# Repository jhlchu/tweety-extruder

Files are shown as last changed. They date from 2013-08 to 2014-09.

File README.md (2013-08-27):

Tweety Extruder
===============

A compact direct-drive extruder for the Prusa i3 Mendel RepRap 3D printer.

Description
-----------

Gain a little extra height on your Prusa i3 with this simple direct drive extruder. Requires an inverted "mini" x-carriage or you can use the Universal 24-to-30mm GT2 X-Carriage also included here.

In contrast to the "Compact Extraptor" design (in my Prusa3 fork) the Tweety is meant to be much simpler. It has no separate mounting and requires no long back-to-front screws. Instead of mounting with nuts on the screw posts, the clamp is secured with screws from the front. The SCAD is highly simplified, as well. All components are aligned with reference to the central point where the gear and bearing grab the filament.

The SCAD is set up by default for a 2engineers 50:1 geared stepper motor, MK7 filament drive gear, 3mm filament, and a 608 idler bearing. As a highly parametric SCAD it should be relatively easy to adapt for your specific motor and dimensional preferences.

Assembly
--------

Print the parts, then connect them in the following order:

* First: Insert M3 locknuts deep into the nut traps in the extruder body.
* Assemble the idler with the axle and a 608 bearing.
* Attach the idler to the body with an M3x20mm bolt or 3mm filament.
* Add idler tensioner shoulder bolts, 2x M3x30mm, with nuts
* Attach the motor to the body with 2x M3x15mm bolts
* Insert the hot-end into the extruder.
* Add a short M3 bolt to the fan mounting hinge.
* Attach the fan to the fan mount.
* Attach the hot-end clamp and fan mount with 2x M3x30mm bolts.
* Attach the assembled extruder to the x-carriage with 3x short M3 bolts.

Customizing the SCAD
--------------------

This SCAD has lots of tunable parameters. You can change the filament width, motor size, idler axle offset, mounting height, and much more. Most parameters can be altered and produce a usable object, but there may be a few that create some weird results. Experiment and let me know if you need help.

As usual, all the parts that will come into contact with the hot-end must be printed in ABS (or any heat-tolerant material).

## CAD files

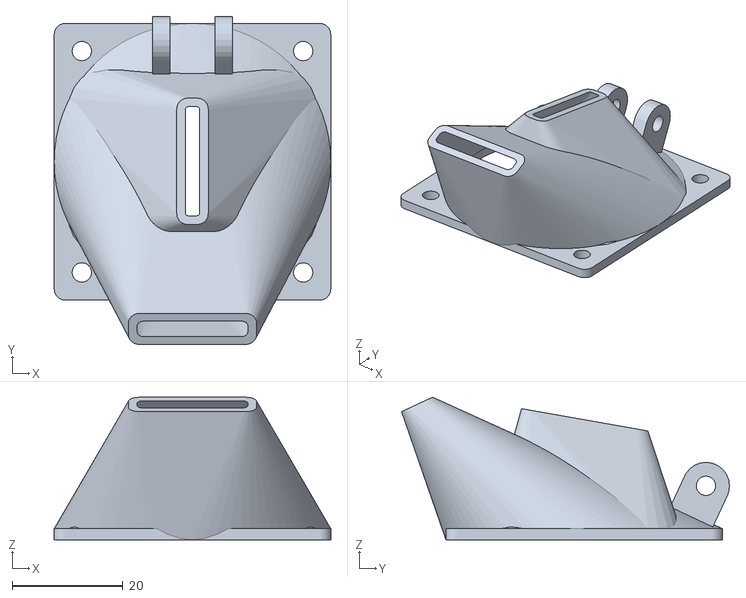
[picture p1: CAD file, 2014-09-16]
output/tweety-fan-duct-only.stl
50.0 x 59.3 x 25.8

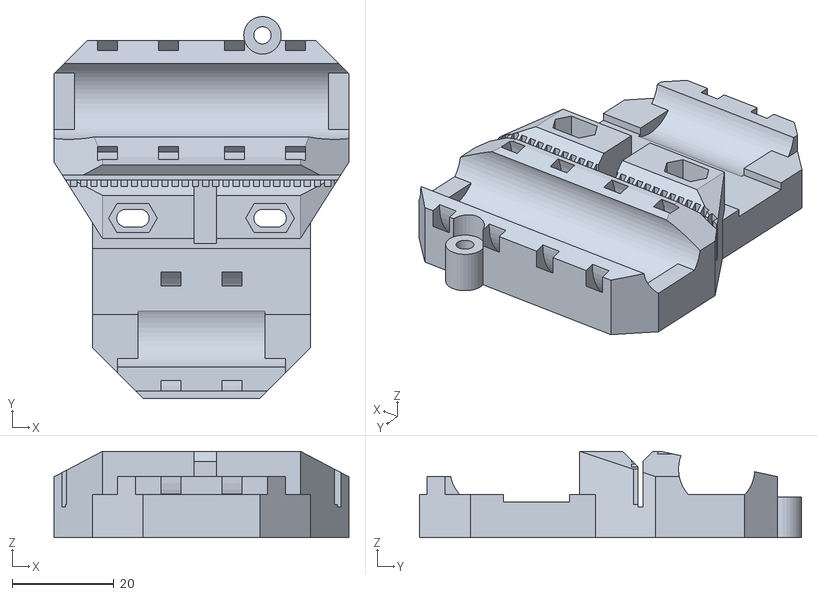
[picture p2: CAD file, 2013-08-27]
x-carriage-24to30-gt2.stl
58.0 x 75.2 x 17.0

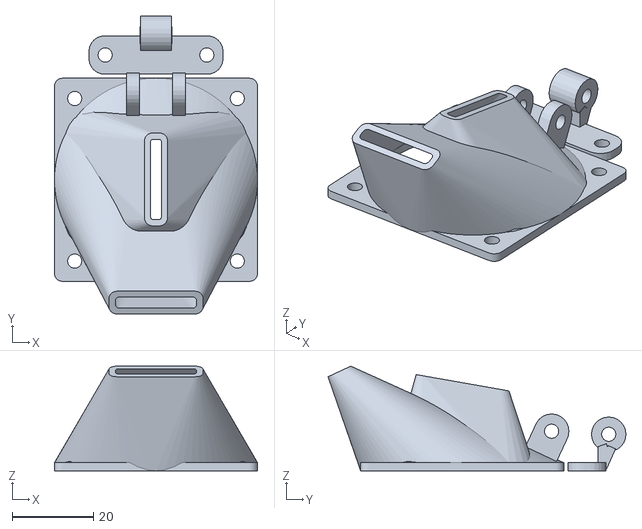
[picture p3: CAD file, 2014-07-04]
output/tweety-fan-duct.stl
50.0 x 73.3 x 25.8

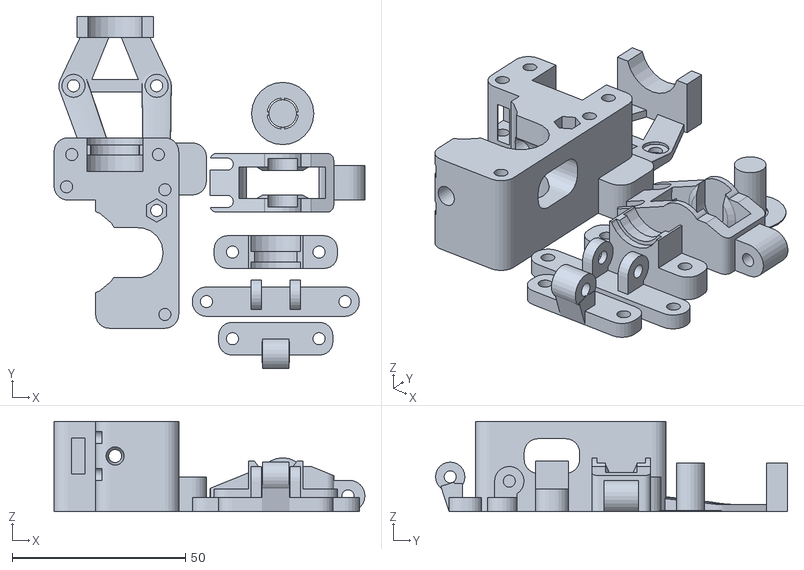
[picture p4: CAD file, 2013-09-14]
output/tweety-plus-all.stl
89.8 x 101.6 x 26.1

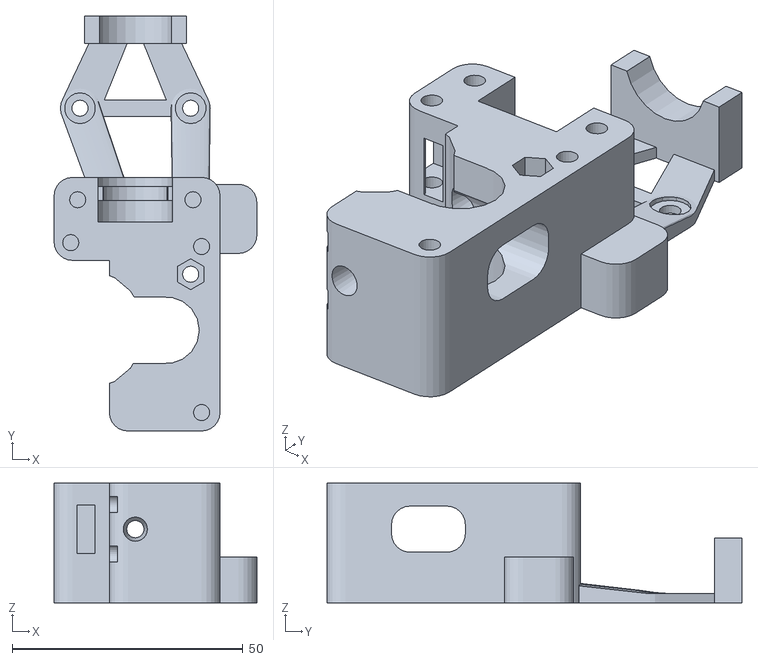
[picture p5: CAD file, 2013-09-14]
output/tweety-plus-body.stl
44.0 x 90.0 x 26.0

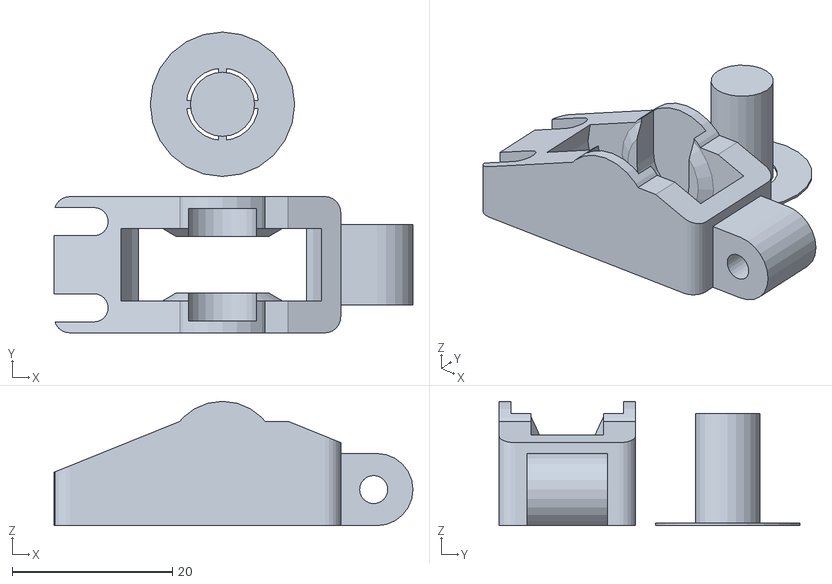
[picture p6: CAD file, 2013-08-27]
output/tweety-idler.stl
44.8 x 37.5 x 15.5

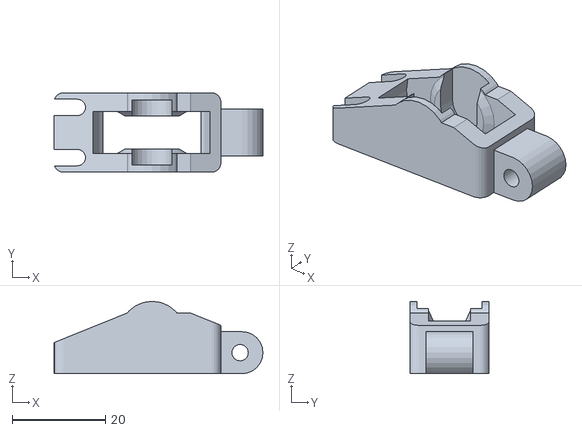
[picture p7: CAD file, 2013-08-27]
output/tweety-idler-no-axle.stl
44.8 x 17.0 x 15.5

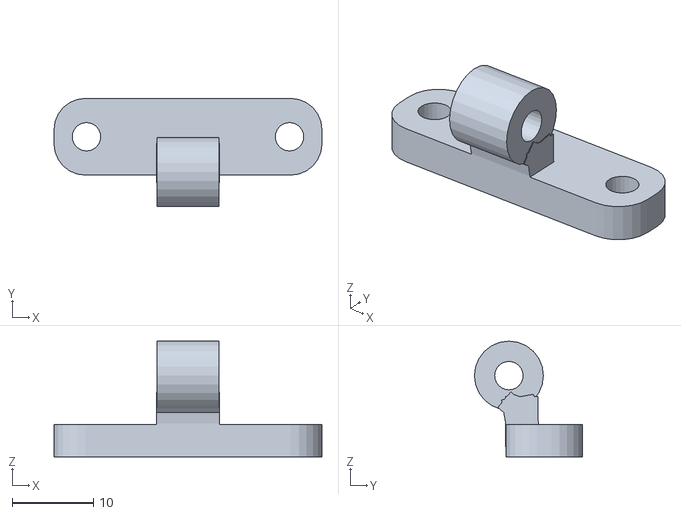
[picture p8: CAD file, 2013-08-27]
output/tweety-fan-hinge.stl
33.0 x 13.3 x 14.3

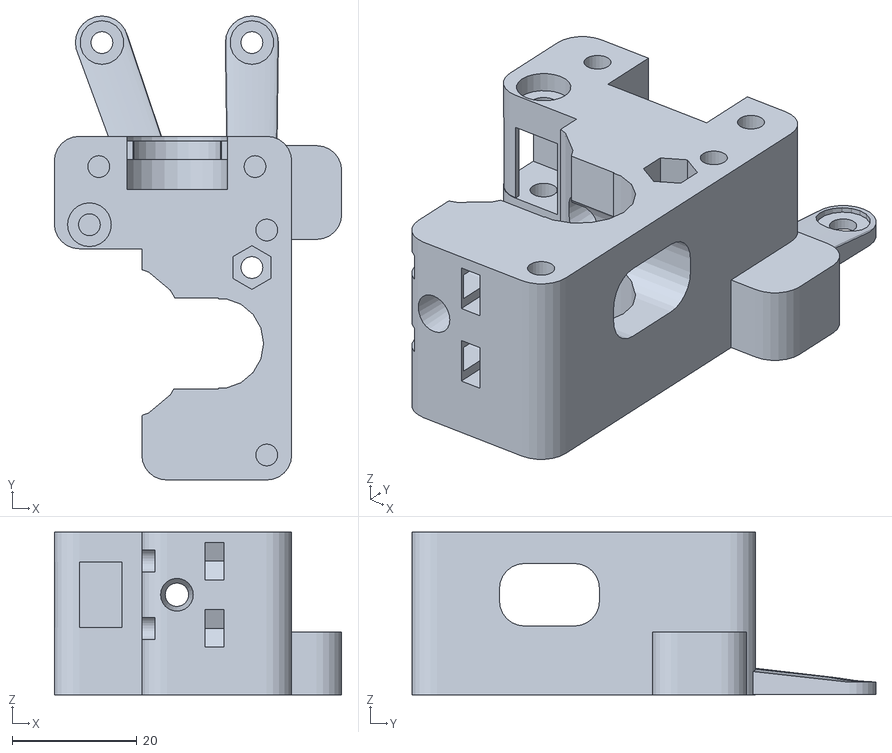
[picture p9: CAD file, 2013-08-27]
output/tweety-body.stl
46.0 x 74.2 x 26.0

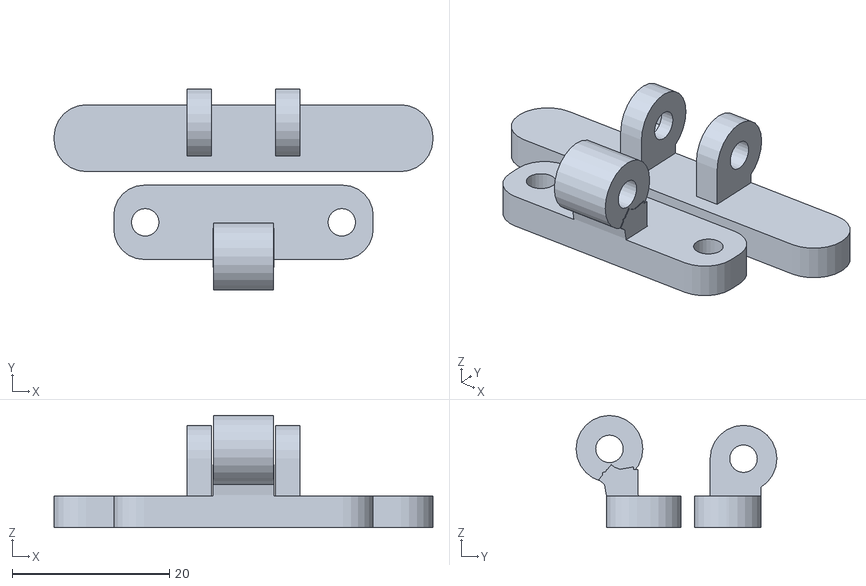
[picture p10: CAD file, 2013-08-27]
output/tweety-fan-mount.stl
48.2 x 25.6 x 14.3

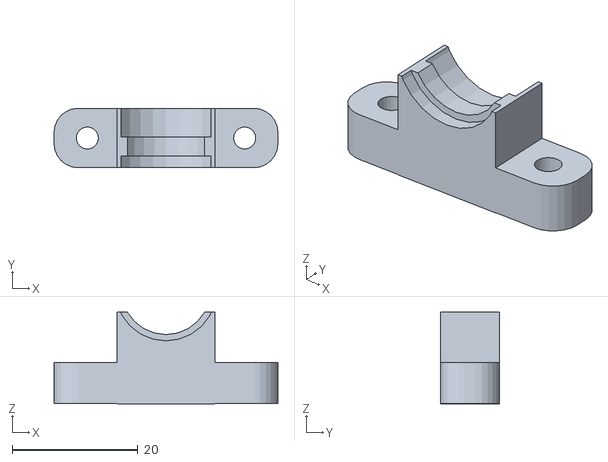
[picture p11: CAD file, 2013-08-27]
output/tweety-clamp.stl
35.6 x 9.45 x 14.6

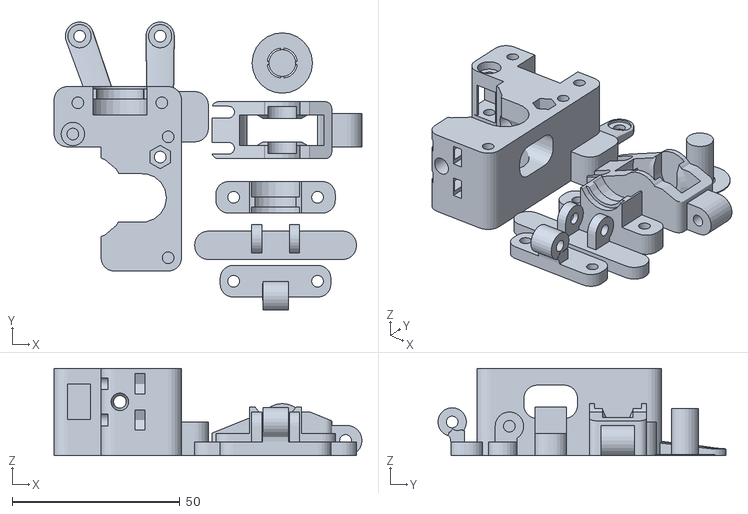
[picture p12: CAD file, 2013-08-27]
output/tweety-all.stl
91.8 x 85.8 x 26.1

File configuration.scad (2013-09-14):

$fn=24;

// Standard screws with slightly wider holes
hole_slop = 0.25;
radius3mm = 1.5;
radius4mm = 2.0;
radius8mm = 4.0;
hole_3mm = radius3mm + hole_slop;
hole_4mm = radius4mm + hole_slop;
hole_8mm = radius8mm + hole_slop;
nut_3mm = radius3mm * 2 + hole_slop + 0.1;
nut_4mm = radius4mm * 2 + hole_slop;
nut_8mm = radius8mm * 2 + hole_slop;

radius608zz = 11;
width608zz = 7;

// The filament gear on the motor
gear_diam = 10.5;
gear_height = 11;

// The hot end
hotend_length = 65;
hotend_diam = 15.9 + 0.2;
hotend_r = hotend_diam / 2;

// Hot end top
hotend_groove_depth = 1;
hotend_above = 4.7;
hotend_groove = 3;
hole_depth = hotend_above + hotend_groove + 2;

// Extruder Block
block_thickness = 20;
standoff_distance = 6;
thicken_block = standoff_distance;
total_thickness = block_thickness + thicken_block;

// Idler
idler_axle_offset = 1;

// Filament
filament_diam = 2.75;
fil_r = filament_diam/2;
filament_hole = fil_r + 0.25 + hole_slop;

// Motor
motor_width = 44;
motor_hole_dist = 36;
motor_height = motor_width;
axle_center_x = 10.25;
motor_axle_x_offset = motor_width/2-axle_center_x;

// X Carriage
x_carriage_holes = 24;

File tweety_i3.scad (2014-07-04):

//
// Tweety Parametric Direct-Drive Extruder
// by Thinkyhead
//
// GPL v3 license
//
// A simple direct drive extruder for the Prusa i3
// Requires Universal or inverted mini x-carriage
//
// The "Universal" x-carriage accepts mounting from 24mm to 30mm and
// has a third hole at X=-12, Z=-36, just like the "mini" x-carriage,
// when mounted with the third hole at the top.
//
// Currently set up for an MK7 gear and 2engineers 50:1 geared stepper motor,
// but should be able to accommodate many dimensional changes.
//

include <configuration.scad>

draw_assembled = false;
draw_body = true;
draw_clamp = true;
draw_idler = true;
draw_axle = true;
draw_fan_mount = true;
draw_fan_duct = true;
endstop_bumper = 8;
nozzle_stabilizer = false;

carriage_pos = [16.5,0,-24]; // for the universal GT2 carriage

nozzle_tip_z = 66;
nozzle_top_z = nozzle_tip_z - hotend_length;

bt2 = block_thickness/2;
sd2 = standoff_distance/2;
mw2 = motor_width/2; mh2 = motor_height/2;
gear_r = gear_diam/2;

below_motor_height = 11;
above_motor_height = 7;
bottom_height = below_motor_height + above_motor_height;
bottom_width = 36;
bot_offset_x = mw2 - bottom_width / 2;
bottom_pos = [bot_offset_x,-sd2,-motor_height/2-bottom_height/2+above_motor_height];

motor_offset_x = -axle_center_x + gear_r + fil_r;
motor_offset_z = 49 - nozzle_top_z;
extruder_z_center = motor_offset_z - below_motor_height / 2;

block_height = motor_height + below_motor_height;
total_thickness = block_thickness + thicken_block;

filament_pos = [0,bt2+standoff_distance,0]; // center the filament in the block
block_pos = filament_pos + [motor_offset_x,0,motor_offset_z]; // move the block for the filament
hotend_hole_pos = filament_pos + [0,0,extruder_z_center-block_height/2+hole_depth];
fil_in_block_pos = [-block_pos[0],0,0];
bearing_in_block_pos = fil_in_block_pos + [-radius608zz,0];

clamp_front_depth = 8;
clamp_gap = 1.5;
clamp_flatten = 3.5;
clamp_screw_len = 25;
clamp_widen = true;
clamp_total_depth = clamp_front_depth + bt2;
clamp_pos = hotend_hole_pos + [0,bt2+clamp_total_depth/2-(bt2),-hole_depth/2];
clamp_in_block_pos = clamp_pos - block_pos;
clamp_hole_dist = false ? 25/2 : floor((hotend_r + hole_3mm + 3) * 2) / 2;
echo("Clamp Hole Distance: ", clamp_hole_dist*2);

mount_holes = [[12,36],[x_carriage_holes/2,0],[-x_carriage_holes/2,0]];

// Idler stuff
idler_bearing_clearance = 2;
idler_perimeter = 5;
idler_width = width608zz + idler_perimeter * 2;
idler_base_height = (radius608zz + idler_bearing_clearance + idler_perimeter - 2) * 2 - 2.5;
idler_height = idler_base_height + 12.5;
idler_depth = radius8mm*2 + idler_perimeter;
idler_uses_groove = idler_axle_offset > 0;
idler_axle_length = idler_width + (idler_uses_groove ? -3 : 0.1);
hinge_width = 10;
hinge_length = idler_depth - 4;
hinge_depth = idler_depth - 4;
hinge_offset = 0;
hw = hinge_width + 0.5;

fan_mount_thickness = 2.0;
fan_duct_base = 2.0;

//
// Assembled and printable rendering
//

if (draw_assembled) {
  //reference_points();
  difference() {
    union() {
      // position the carriage with its holes at [0,0]
      %translate(carriage_pos) rotate([90,0,0]) import("x-carriage-24to30-gt2.stl");

      // the structure between the extruder and carriage is static
      extruder_standoffs();

      // The body follows the filament path
      translate(filament_pos) {
        // the filament
        %translate([0,0,extruder_z_center]) the_filament();
        translate([0,0,-nozzle_top_z/2]) %the_nozzle(); // the nozzle is fixed to the bottom
      }
      translate(block_pos) { // motor and body move around the filament & gear, nozzle top
        extruder_body();
        translate(clamp_in_block_pos) extruder_clamp();
        if (draw_fan_mount || draw_fan_duct)
          translate(clamp_in_block_pos + [0,clamp_front_depth + fan_mount_thickness - 0.8,0])
            rotate([180,-90,-90])
              fan_mount();
        translate(bearing_in_block_pos) idler_body();
        %translate([0,bt2]) motor_dummy();
      }
    }
    // Carriage holes and motor holes
    carriage_holes();
    translate(block_pos) {
      motor_holes();
      translate(bearing_in_block_pos) idler_holes();
    }

    // Clamp Holes
    translate(clamp_pos) clamp_holes();
  }
} else {
  // Draw everything ready-to-print
  translate([-40,-10]) {

    if (draw_body)
      translate([0,draw_fan_duct ? -35 : -10,total_thickness/2+sd2]) rotate([90,0]) {
        difference() {
          union() {
            extruder_body();
            translate(-block_pos) extruder_standoffs();
          }
          translate(-block_pos) carriage_holes();
          motor_holes();
          translate(bearing_in_block_pos) idler_holes();
          translate(clamp_in_block_pos) clamp_holes();
        }
        idler_support();
      }

    if (draw_clamp)
      translate([50,0,clamp_total_depth/2]) rotate([-90,0]) {
        difference() {
          union() { extruder_clamp(); }
          clamp_holes();
        }
      }

    if (draw_idler)
      translate([52,20,idler_axle_offset+idler_depth/2]) rotate([0,-90]) {
        difference() {
          idler_body();
          idler_holes();
        }
      }

    if (draw_fan_mount || draw_fan_duct) translate([50,-15,fan_mount_thickness/2]) {
      rotate([0,0,90]) {
        if (draw_fan_mount) {
          rotate([0,180,0]) difference() {
            fan_mount(mode=1);
            rotate([90,180,90]) clamp_holes();
          }
        }
        translate([-hole_depth-1,0,0]) fan_mount(mode=2);
      }
    }
  }
}

//
// Extruder Body
//

module extruder_body() {
  gear_clearance = 2;
  check_window = 16;
  cube_reduce = 20;
  offs = thicken_block / 2;
  thik = total_thickness;

  difference() {
    union() {
      // The "upper block" - motor mount, filament drive
      translate([cube_reduce/2,-offs,-below_motor_height/2]) // the middle point of the upper block
        rotate([90,0]) rounded_cube([motor_width-cube_reduce,block_height,thik], r=4, center=true);

      // The "lower block" - symmetrical around the nozzle, based on a bottom width
      translate(bottom_pos) // bottom-justify
        rotate([90,0]) rounded_cube([bottom_width,bottom_height,thik], r=4, center=true);

      // An endstop bumper
      if (endstop_bumper > 0)
        translate(bottom_pos + [bottom_width/2,-total_thickness/2+10/2,0])
          rotate([90,0]) rounded_cube([endstop_bumper*2,15,10], r=4, center=true);
    }

    // Opening for the gear
    translate([axle_center_x,-offs,0.15]) rotate([90,0,0]) cylinder(r=gear_r+gear_clearance,h=thik+0.1,center=true,$fn=18);

    // Cleanup nearby
    translate([axle_center_x-(gear_r+gear_clearance),-offs,0.15]) cube([(gear_r+gear_clearance)*2,thik+0.1,(gear_r+gear_clearance)*2],center=true);

    // 608 bearing and its clearance
    translate(bearing_in_block_pos)
      rotate([90,0,0]) {
        if (draw_assembled) %bearing608();
        // %hollow_cylinder(r1=radius608zz,r2=radius8mm,h=8,center=true,$fn=36);
        translate([0,0,offs]) cylinder(r=radius608zz+gear_clearance,h=thik+0.1,center=true,$fn=18);
      }

    // Idler Hinge Space
    translate(bearing_in_block_pos)
      rotate([90,0,90])
        translate([-hinge_offset,-idler_base_height/2-hinge_length/2,-idler_axle_offset-1])
          translate([0,0,-idler_depth/2+hinge_depth/2])
            cube([hw,hinge_length+0.25,hinge_depth+3.5],center=true);

    // Gear Check
    translate([mw2,0,0]) rotate([0,90,0]) rounded_cube([check_window,10,100], r=4, center=true);

    // Filament Through Hole
    assign(rad=filament_hole,funnel_size=10)
    translate(fil_in_block_pos) {
      cylinder(r=rad, h=block_height, center=true);
      translate([0,0,motor_height/2-funnel_size/2]) cylinder(r1=rad, r2=rad+0.75, h=funnel_size, center=true);
      translate([0,0,-funnel_size/2-check_window/2+0.5]) cylinder(r1=rad, r2=rad+1.5, h=funnel_size, center=true);
    }

    // Nozzle Hole
    translate(fil_in_block_pos + [0,0,-block_height/2-below_motor_height/2+hole_depth])
      groovemount_cutouts();

  } // difference
}

module extruder_standoffs() {
  frac = 3;
  h = standoff_distance / frac;
  z = (standoff_distance - h) / 2;
  rotate([90,0,0]) {
    translate([0,0,-sd2]) {
      hull() { // top-left to bottom-left
        translate(mount_holes[0]) cylinder(r=hole_3mm+2, h=standoff_distance, center=true);
        translate(mount_holes[1]) translate([0,0,z])
          cylinder(r=hole_3mm+2.5, h=h, center=true);
      }
      hull() { // top-right to bottom-right [-4.5,60,sd2]
        translate([0,36-2]) cylinder(r=hole_3mm+2, h=standoff_distance, center=true);
        translate(mount_holes[2]) translate([0,0,z])
          cylinder(r=hole_3mm+2.5, h=h, center=true);
      }
      if (thicken_block < standoff_distance) hull() { // top-left to top-right
        translate(mount_holes[0]) cylinder(r=hole_3mm+2, h=standoff_distance, center=true);
        translate([0,36]) cylinder(r=hole_3mm+2, h=standoff_distance, center=true);
      }
    }
  }
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

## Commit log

2013-09-11 Added an optional nozzle stabilizer, fixed the nozzle hole.
    The stabilizer limits how far the nozzle can be pulled downward by a
    collision when the Y bed is moving from front-to-back.
    [tweety_i3.scad]
2013-09-14 Take 2mm off BR, fix groove position, remove screw recess, deepen motor screw holes
    [configuration.scad, tweety-plus-all.stl, tweety-plus-body.stl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]
2014-07-04 Configurable fan duct with top and bottom blowers.
    [tweety-fan-adapt.stl, tweety-fan-duct.stl, tweety_i3.scad]
2014-09-16 Add the fan duct STL.
    [tweety-fan-duct-only.stl]
